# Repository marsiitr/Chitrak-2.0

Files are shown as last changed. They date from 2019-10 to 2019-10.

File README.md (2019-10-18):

# Chitrak-2.0

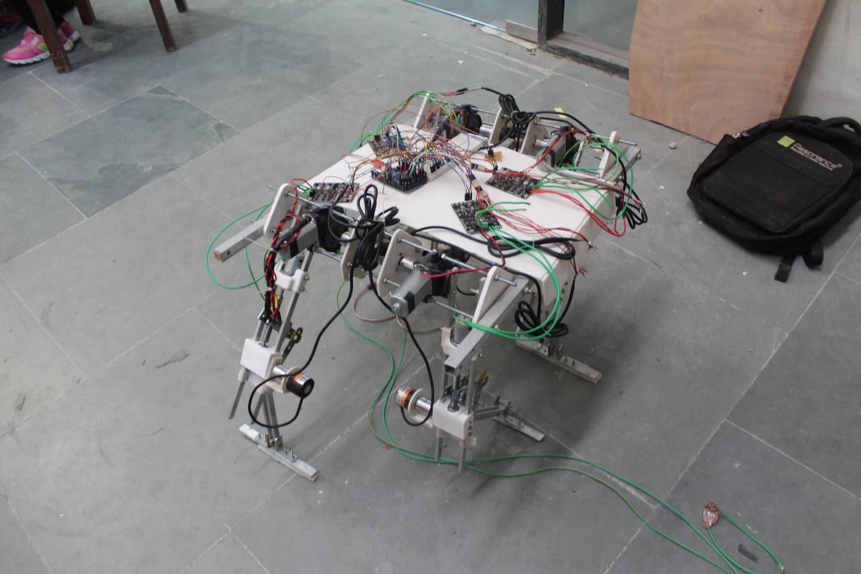
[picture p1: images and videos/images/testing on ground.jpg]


## **Abstract-:**

Chitrak is aimed to be a dynamically stable quadruped robot. With the hopes that it will be able to serve as a robotic cat to accompany soldiers in terrain too rough for conventional vehicles and provide aid to people during natural calamities when conventional vehicles prove to be less usable. Chitrak uses four legs for movement, allowing it to move across surfaces that would defeat wheels.
<br/>

## **Motivation:**

* The current robots being used are very expensive.
* The runtime of the current robots is very less. And on a single charge they cannot be deployed for practical use by the military. 
* Also, when standing, these robot consume energy which can be avoided to increase the runtime.
* Package delivery during Natural disasters can be faster and efficient. 
* Soldiers will be able to carry more food & ammunition during combat missions.
<br/>

## **Mechanical Aspect of the Design:**
As we are designing a fully actuated quadruped so in our first design basically we have used two motors for actuating each joint(hip and knee)of a leg. In the beginning, our main aim was to build quadruped which is both cost effective and energy efficient. So, for that purpose we used a worm geared motor which has a self locking property because of worm gear which can only be able to rotate using worm and so it cannot be back-driven. So it's main advantage will be it does not need to be operating to work against gravity in static position.

<br/>

Next placing both the motors at the hip is self beneficiary as it reduces the amount of torque hip motor has to apply to lift the legs, so  we have mounted both motors on hip. Also for power transmission for motor to  actuate knee joint we have used a timing belt pulley system (as it will have less weight and  it effectively transfers the load). Now on seeing the actual leg motion during walking we see that the upper leg is moving in the direction of gravity while lower leg against it mostly. Therefore we required larger torque to move the lower leg than upper by calculating the approximate torques we have reached on conclusion of using a 1:4 gear ratio belt pulley system so as to increase torque on knee joints

<br/>

Further we have used aluminium links for constructing it ,some 3d printed parts for joints, mountings and 3d printed pulleys. There are two parallel links that are connected through nuts and bolts to provide more stiffness and strength to the structure for upper and lower leg. Rotary encoders are used as a sensors to provide feedback about the position of legs they are mounted on hip joints coupled to each motor. For end effector we used a broad padded plate in order to provide more surface area for better traction. The two front legs are joined using 6mm threaded rod, same is for back legs and these two parts are joined with alumininum channel to construct a body on which whole electronics system is being placed.

<br/>

The problem with this design was that the Belt-Pulley mechanism failed while testing the quadruped on ground. The timing belt was slipping on the upper pulley due to load on the leg during the gait cycle. This slipping changed the angle between the upper and lower leg to an arbitrary value and the whole cycle would get disrupted. 

<br/>

In the current design, we used a lead screw mechanism to drive the lower leg. In it, an 8-cm long lead screw is placed parallel to the upper leg (thigh) and a link is attached to its nut which drives the lower leg. So, the linear motion of the nut on lead screw gets converted to rotational motion of lower leg about the knee joint. Since lead screw mechanism is self locking upto very large amount of load, it can bear the impact loading during the gait cycle and overcomes the problem faced in the previous design.

<br/>

Upper leg in actuated by the same worm-geared motor. Lead Screw is powered by a 900RPM DC geared motor to provide sufficient speed for driving the lower leg. This motor is mounted on the upper leg by a 3D printed part, 'Motor Mount' (solidworks file) containing cavities for the parallel links. Knee joint is also made with 3D printed part, 'Revolute Joint', which contains link spaces and cavities for two radial ball bearings on either side for holding the shaft. A machined Aluminium part is used to couple the lower leg to knee shaft. A Rotary Encoder is also coupled with the Knee Shaft for feedback of the angle between upper and lower leg.

<br/>

## **Electronics Aspect of the Design:**

Chitrak is powered by 4 LiPo batteries(1 for each leg) driving 8 Worm-Gear 500 RPM motors. Each leg has 2 DOF with two actuators (one for the hip joint, and one for each knee joint), for a total of 8 motors. For a single leg, there are 2 active legs joint. The knee joint is rotated by the actuator mounted at hip joint through the belt. Each actuator unit consists of a rotary encoder attached to it for angle measurement.

<br/>

In our first prototype of one leg, we first simulated the motion of the leg on Matlab. By taking the trajectory of the end-effector to be a semi-ellipse (which is the approximate trajectory of natural leg motion), we applied inverse kinematics on the end-effector by considering an X-Y reference frame on the hip joint and varied the joint angles accordingly. For smooth motion, we used Spline for trajectory planning taking the acceleration to be zero. On physical implementation, the leg worked as expected with the end-effector following an ellipse and leg mimicking the motion similar to that of a four-legged animal.

<br/>

For the trajectory, for self-coordinated movement of the four legs, we are using the method of. 2D inverted pendulum method for alternate legs. It consists of the center of mass (CoM) and massless telescopic leg. We measure the inclination of the pendulum θ from vertical, positive for counterclockwise rotation. This yields us the horizontal dynamics of the CoM. The kick force f = Mg/ cos θ always balance with the gravity acting on the point mass. Time for transfer and support leg exchange movement is easily obtained by solving the differential equations of orbital energy and force. Solving these equations helps us to generate the walking pattern generation according to the corresponding gait cycle.

<br/>

For coordinating motion of all three legs, one leg is lifted from the ground at a time and rest of legs are moving in straight line. Thus a straight line has to be broken into 3 parts, and each leg traverses in a different part of straight line while another leg is completing elliptical motion.

<br/>

## **Estimated Budget:**

The Design of Kitty is made with the main focus on lightweight, high endurance and low cost. Most of the components used in the bot are easily accessible. The current estimated cost of Kitty is around 53000 INR. The cost can be significantly reduced when the bot is manufactured commercially on a large scale. It is cheap, easy to reproduce, robust, and safe to handle. This makes it an excellent tool for research of multi-segment legs in quadruped robots.

---------------------------------------------------------
|Component 		 |	Cost(INR) |	Total	 |
|---|---|---|
|Worm Geared Motor (x8)	|	1552 	 |	12417	 |
|LiPo Battery(x5) 	 |	1309 	 |	6545	 |
|Rotary Encoder(x8) 	  |	1590 	 |	12720	 |
|Arduino Uno(x5) 	 |	425 	 | 2125 |
|Cytron Motor Driver(x4)|	1890 	 |	7560	 |
|PCB (x1) 		 |	1000 	 |	1000	 |
|MPU6050 (x2) 		 |	150 	 |	300	 |
|Ultrasonic Sensor (x2) |	197 	 |	394	 |
|Jumper Wires 		|	5 	 |	150	 |
|Square Channels (x20ft)|	20 	 |	400	 |
|Aluminum Links (x12ft) |	20 	 |	320	 |
|Chain & Sprocket (x4) 	|	400 	 |	1600 	|
|3D Printed Parts (x4) 	|	1500 	 |	6000 	|
|Miscellaneous 	 	|	800 	 |	1000	 |
|Total 			 |		 |	52531 |
<br/>

## **Applications:**
* Travel in rough terrains where conventional vehicles have low mobility.
* Carry payloads for soldiers in Combat operations for long duration.
* Provide aid to soldiers during combat operations without loss of human lives.
* Deploy food and medicines to people stuck in inaccessible areas during natural disasters.
<br/>

## **Limitations:**

* Obstacle detection has not been included.
* IMU has not been implemented for self balancing in rough terrain.
* Currently movement of robot is restricted to 1 dimension only.
<br/>

## **Future Goals:**

* Increase Runtime of the Robot after a single charge.
* Obtain Pace, Gallop and Canter Gait cycle for faster movement.
* Increase the Payload Capacity of the Robot.
* Provide 3 DOF to each leg providing more flexibility to the robot.
* Using Computer Vision for Obstacle detection, human recognition and corresponding Path planning.
* Provide 3 DOF to each leg providing more flexibility to the robot.   
<br/>

## **Team Members:**

* Avdesh Ranwa
* Dhruv Sehgal
* Harshil Patel
* Ujjwal Baranwal 
* Yawan Gupta
<br/>

## **Mentros:**

* Divyansh Gupta
* Nitin Yadav
* Prashant Kumar
* Vishal Singh
<br/>

## **References:**
---------------------------------------------------------------------------------
|Name				 |	Author				 	|
|---|---|
|Research of Mammal BionicQuadrupedRobots 	 |Yibin Li, Bin Li, Jiuhong Ruan, and Xuewen Rong Quadruped Walking Robots at Tokyo Institute of	Technology Design, Analysis, and Gait Control Methods SHIGEO HIROSE, YASUSHI FUKUDA, KAN YONEDA, AKIHIKO NAGAKUBO, HIDEYUKI TSUKAGOSHI, KEISUKE ARIKAWA, GEN ENDO, TAKAHIRO DOI, AND RYUICHI HODOSHIMA|
|Kinematic Modeling of Quadruped Robot		 |Smita A. Ganjare, V S Narwane & Ujwal Deole	  |
|Inverse Kinematic Analysis Of A QuadrupedRobot 	  |Muhammed Arif Sen, Veli Bakırcıoğlu, Mete Kalyoncu|
|Introduction to Robotics	 |John J. Craig		 |
|Robot Dynamics and Control	 |Mark W. Spong, M. Vidyasagar, Seth Hutchinson  |

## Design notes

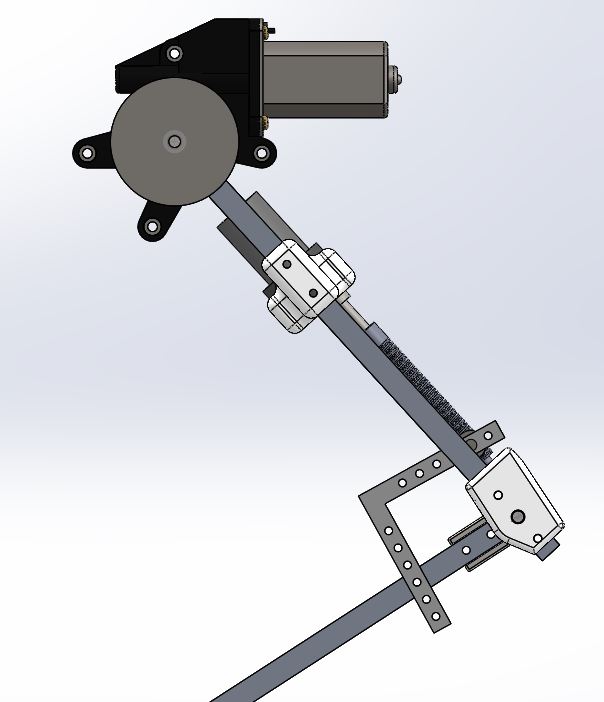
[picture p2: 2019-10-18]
images and videos/images/leg design.jpeg

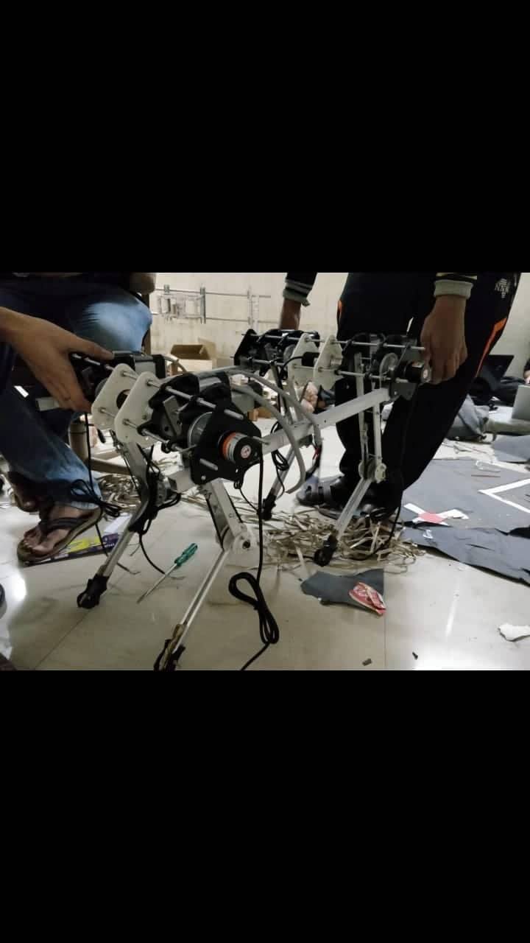
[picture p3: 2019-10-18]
images and videos/images/second design.jpg

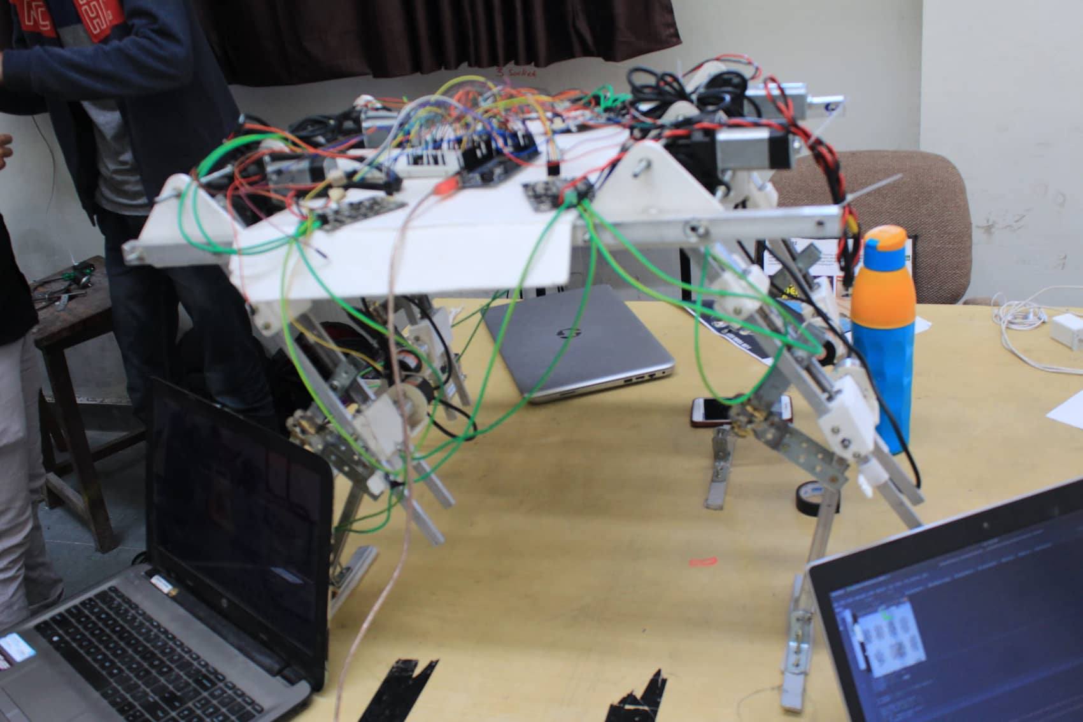
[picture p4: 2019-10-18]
images and videos/images/chitrak current design.jpg

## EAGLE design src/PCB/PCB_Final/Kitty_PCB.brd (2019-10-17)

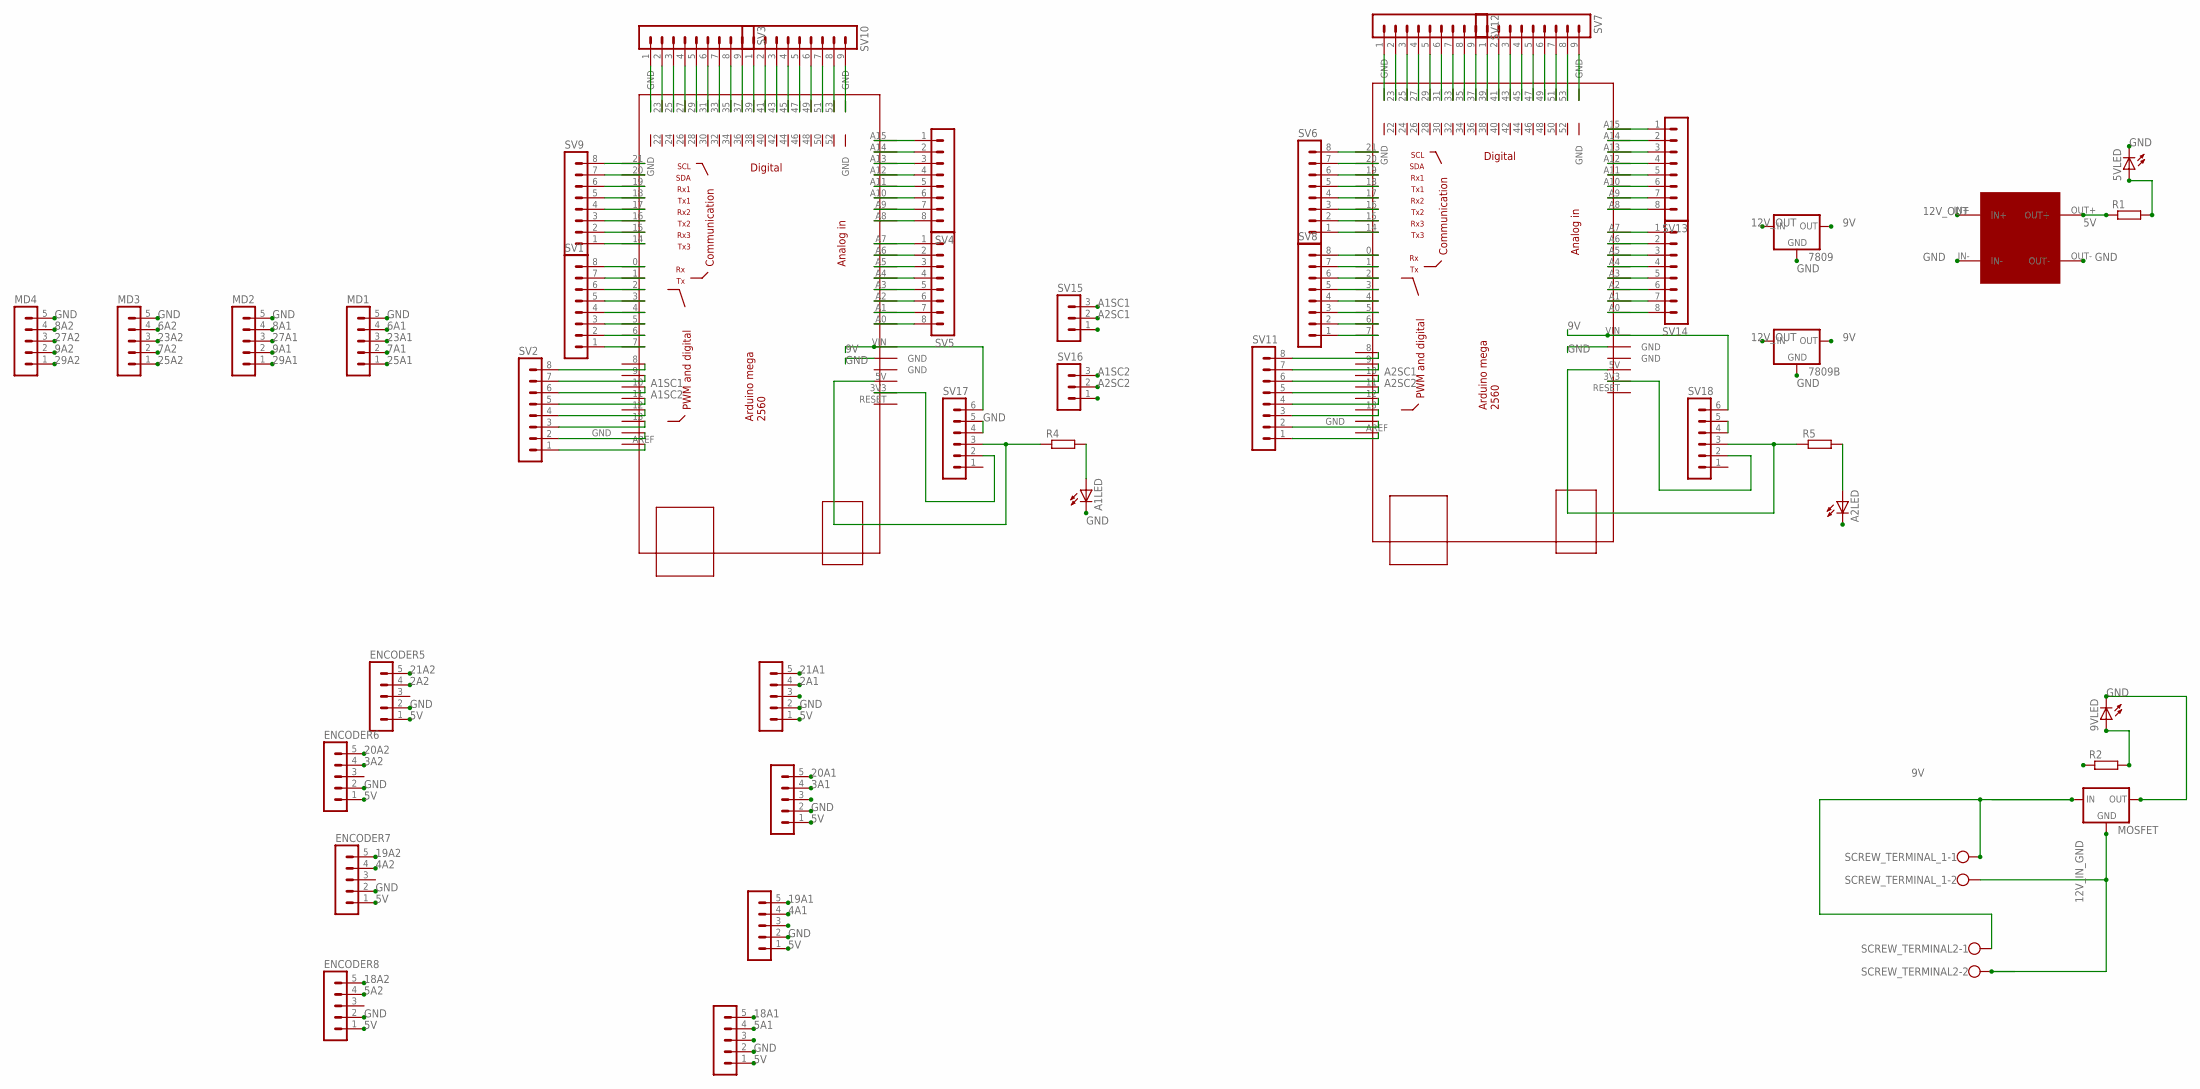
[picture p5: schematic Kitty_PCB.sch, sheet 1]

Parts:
5VLED, 9VLED: LED; LED3MM
7809, 7809B: VOLTAGE_REGULATOR_78XXS; 78XXS
A1LED, A2LED: LED; LED3MM
ARDUINO1, ARDUINO2: MEGA_DEVICE; MEGABOX
ENCODER1, ENCODER2, ENCODER3, ENCODER4, ENCODER5, ENCODER6, ENCODER7, ENCODER8: RELIMATE_05-1; MA05-1
MD1, MD2, MD3, MD4: RELIMATE_05-1; MA05-1
MOSFET: VOLTAGE_REGULATOR_78XXS; 78XXS
R1, R2, R4, R5: RESISTANCE0207/10; 0207/10
SCREW_TERMINAL2: SCREW_TERMINAL_POWER; POWER_CONNECTOR
SCREW_TERMINAL_1: SCREW_TERMINAL_POWER; POWER_CONNECTOR
SV1, SV2, SV4, SV5, SV6, SV8, SV9, SV11, SV13, SV14: RELIMATE_08-1; MA08-1
SV3, SV7, SV10, SV12: RELIMATE_09-1; MA09-1
SV15, SV16: RELIMATE_03-1; MA03-1
SV17, SV18: RELIMATE_06-1; MA06-1
U$1: BUCK_CONVERTER

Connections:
0A1: ARDUINO1.0, SV1.8
0A2: ARDUINO2.0, SV8.8
1A1: ARDUINO1.1, SV1.7
1A2: ARDUINO2.1, SV8.7
2A1: ARDUINO1.2, ENCODER1.4, SV1.6
2A2: ARDUINO2.2, ENCODER5.4, SV8.6
3A1: ARDUINO1.3, ENCODER2.4, SV1.5
3A2: ARDUINO2.3, ENCODER6.4, SV8.5
4A1: ARDUINO1.4, ENCODER3.4, SV1.4
4A2: ARDUINO2.4, ENCODER7.4, SV8.4
5A1: ARDUINO1.5, ENCODER4.4, SV1.3
5A2: ARDUINO2.5, ENCODER8.4, SV8.3
5V: ENCODER1.1, ENCODER2.1, ENCODER3.1, ENCODER4.1, ENCODER5.1, ENCODER6.1, ENCODER7.1, ENCODER8.1, R1.1, U$1.OUT+
6A1: ARDUINO1.6, MD1.4, SV1.2
6A2: ARDUINO2.6, MD3.4, SV8.2
7A1: ARDUINO1.7, MD1.2, SV1.1
7A2: ARDUINO2.7, MD3.2, SV8.1
8A1: ARDUINO1.8, MD2.4, SV2.8
8A2: ARDUINO2.8, MD4.4, SV11.8
9A1: MD2.2
9A2: ARDUINO1.9, ARDUINO2.9, MD4.2, SV2.7, SV11.7
9V: 7809.OUT, 7809B.OUT, ARDUINO1.VIN, ARDUINO2.VIN, R2.1, SV17.6, SV18.6
12A1: ARDUINO1.12, SV2.4
12A2: ARDUINO2.12, SV11.4
12V_IN_GND: MOSFET.GND, SCREW_TERMINAL2.2, SCREW_TERMINAL_1.2
12V_OUT: 7809.IN, 7809B.IN, MOSFET.IN, SCREW_TERMINAL2.1, SCREW_TERMINAL_1.1, U$1.IN+
13A1: ARDUINO1.13, SV2.3
13A2: ARDUINO2.13, SV11.3
14A1: ARDUINO1.14, SV9.1
14A2: ARDUINO2.14, SV6.1
15A1: ARDUINO1.15, SV9.2
15A2: ARDUINO2.15, SV6.2
16A1: ARDUINO1.16, SV9.3
16A2: ARDUINO2.16, SV6.3
17A1: ARDUINO1.17, SV9.4
17A2: ARDUINO2.17, SV6.4
18A1: ARDUINO1.18, ENCODER4.5, SV9.5
18A2: ARDUINO2.18, ENCODER8.5, SV6.5
19A1: ARDUINO1.19, ENCODER3.5, SV9.6
19A2: ARDUINO2.19, ENCODER7.5, SV6.6
20A1: ARDUINO1.20, ENCODER2.5, SV9.7
20A2: ARDUINO2.20, ENCODER6.5, SV6.7
21A1: ARDUINO1.21, ENCODER1.5, SV9.8
21A2: ARDUINO2.21, ENCODER5.5, SV6.8
23A1: ARDUINO1.23, MD1.3, SV3.2
23A2: ARDUINO2.23, MD3.3, SV12.2
25A1: ARDUINO1.25, MD1.1, SV3.3
25A2: ARDUINO2.25, MD3.1, SV12.3
27A1: ARDUINO1.27, MD2.3, SV3.4
27A2: ARDUINO2.27, MD4.3, SV12.4
29A1: ARDUINO1.29, MD2.1, SV3.5
29A2: ARDUINO2.29, MD4.1, SV12.5
31A1: ARDUINO1.31, SV3.6
31A2: ARDUINO2.31, SV12.6
33A1: ARDUINO1.33, SV3.7
33A2: ARDUINO2.33, SV12.7
35A1: ARDUINO1.35, SV3.8
35A2: ARDUINO2.35, SV12.8
37A1: ARDUINO1.37, SV3.9
37A2: ARDUINO2.37, SV12.9
A1SC1: ARDUINO1.10, SV2.6, SV15.3
A1SC2: ARDUINO1.11, SV2.5, SV16.3
A2SC1: ARDUINO2.10, SV11.6, SV15.2
A2SC2: ARDUINO2.11, SV11.5, SV16.2
GND: 5VLED.K (C), 9VLED.K (C), 7809.GND, 7809B.GND, A1LED.K (C), A2LED.K (C), ARDUINO1.GND@3 (GND), ARDUINO2.GND@3 (GND), ENCODER1.2, ENCODER2.2, ENCODER3.2, ENCODER4.2, ENCODER5.2, ENCODER6.2, ENCODER7.2, ENCODER8.2, MD1.5, MD2.5, MD3.5, MD4.5, MOSFET.OUT, SV17.4, SV17.5, U$1.IN-, U$1.OUT-
unnamed: ARDUINO1.3V3, SV17.2
unnamed: ARDUINO1.5V, R4.1, SV17.3
unnamed: 5VLED.A, R1.2
unnamed: SV18.4, SV18.5
unnamed: ARDUINO2.3V3, SV18.2
unnamed: ARDUINO2.5V, R5.1, SV18.3
unnamed: A1LED.A, R4.2
unnamed: A2LED.A, R5.2
unnamed: 9VLED.A, R2.2
unnamed: ARDUINO1.GND@5 (GND), SV3.1
unnamed: ARDUINO1.GND@1 (GND), SV2.2
unnamed: ARDUINO1.AREF, SV2.1
unnamed: ARDUINO1.A15, SV4.1
unnamed: ARDUINO1.A14, SV4.2
unnamed: ARDUINO1.A13, SV4.3
unnamed: ARDUINO1.A12, SV4.4
unnamed: ARDUINO1.A11, SV4.5
unnamed: ARDUINO1.A10, SV4.6
unnamed: ARDUINO1.A9, SV4.7
unnamed: ARDUINO1.A8, SV4.8
unnamed: ARDUINO1.A7, SV5.1
unnamed: ARDUINO1.A6, SV5.2
unnamed: ARDUINO1.A5, SV5.3
unnamed: ARDUINO1.A4, SV5.4
unnamed: ARDUINO1.A3, SV5.5
unnamed: ARDUINO1.A2, SV5.6
unnamed: ARDUINO1.A1, SV5.7
unnamed: ARDUINO1.A0, SV5.8
unnamed: ARDUINO2.GND@1 (GND), SV11.2
unnamed: ARDUINO2.AREF, SV11.1
unnamed: ARDUINO2.A15, SV13.1
unnamed: ARDUINO2.A14, SV13.2
unnamed: ARDUINO2.A13, SV13.3
unnamed: ARDUINO2.A12, SV13.4
unnamed: ARDUINO2.A11, SV13.5
unnamed: ARDUINO2.A10, SV13.6
unnamed: ARDUINO2.A9, SV13.7
unnamed: ARDUINO2.A8, SV13.8
unnamed: ARDUINO2.A7, SV14.1
unnamed: ARDUINO2.A6, SV14.2
unnamed: ARDUINO2.A5, SV14.3
unnamed: ARDUINO2.A4, SV14.4
unnamed: ARDUINO2.A3, SV14.5
unnamed: ARDUINO2.A2, SV14.6
unnamed: ARDUINO2.A1, SV14.7
unnamed: ARDUINO2.A0, SV14.8
unnamed: ARDUINO1.39, SV10.1
unnamed: ARDUINO1.41, SV10.2
unnamed: ARDUINO1.43, SV10.3
unnamed: ARDUINO1.45, SV10.4
unnamed: ARDUINO1.47, SV10.5
unnamed: ARDUINO1.49, SV10.6
unnamed: ARDUINO1.51, SV10.7
unnamed: ARDUINO1.53, SV10.8
unnamed: ARDUINO1.GND@7 (GND), SV10.9
unnamed: ARDUINO2.GND@5 (GND), SV12.1
unnamed: ARDUINO2.39, SV7.1
unnamed: ARDUINO2.41, SV7.2
unnamed: ARDUINO2.43, SV7.3
unnamed: ARDUINO2.45, SV7.4
unnamed: ARDUINO2.47, SV7.5
unnamed: ARDUINO2.49, SV7.6
unnamed: ARDUINO2.51, SV7.7
unnamed: ARDUINO2.53, SV7.8
unnamed: ARDUINO2.GND@7 (GND), SV7.9

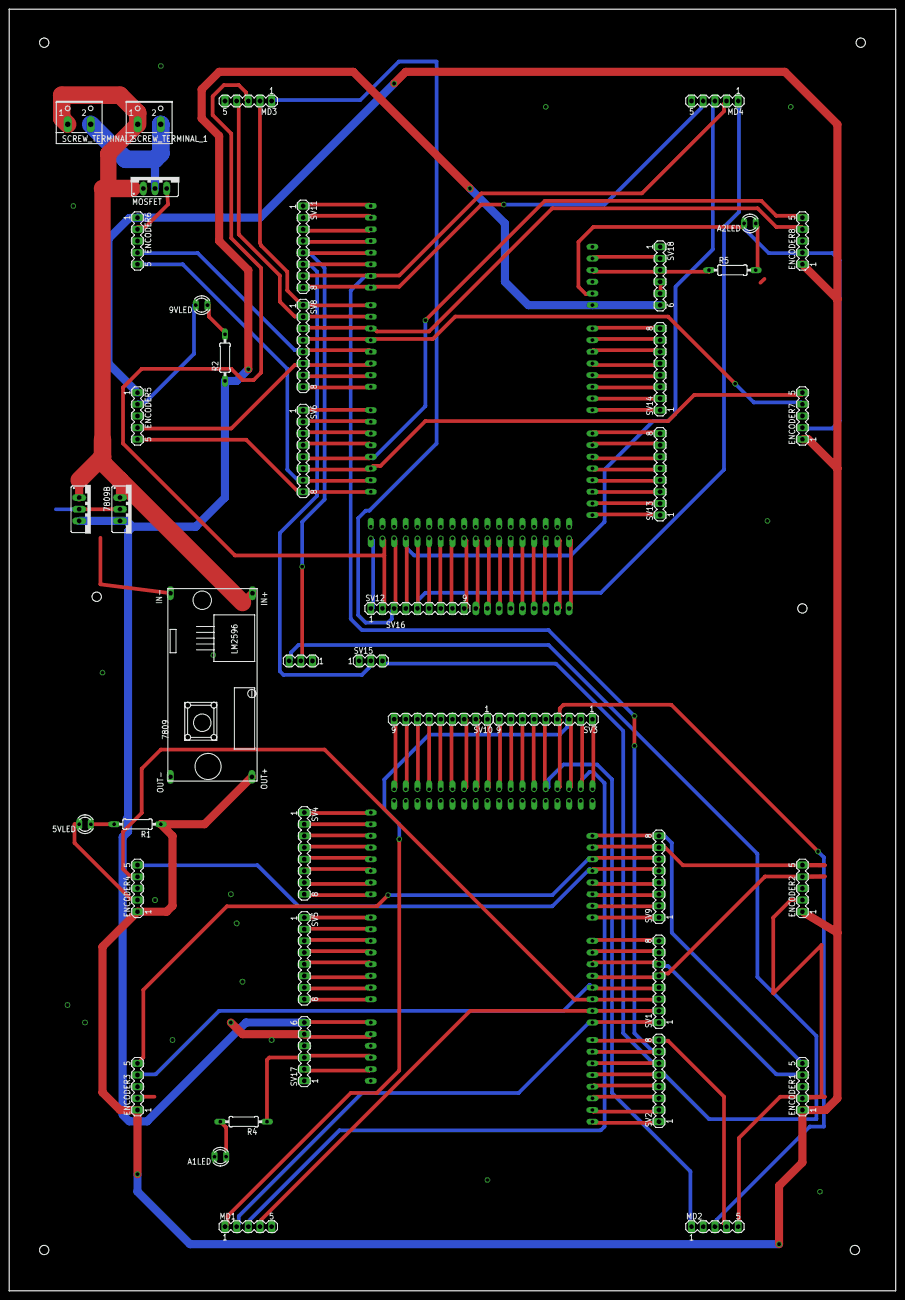
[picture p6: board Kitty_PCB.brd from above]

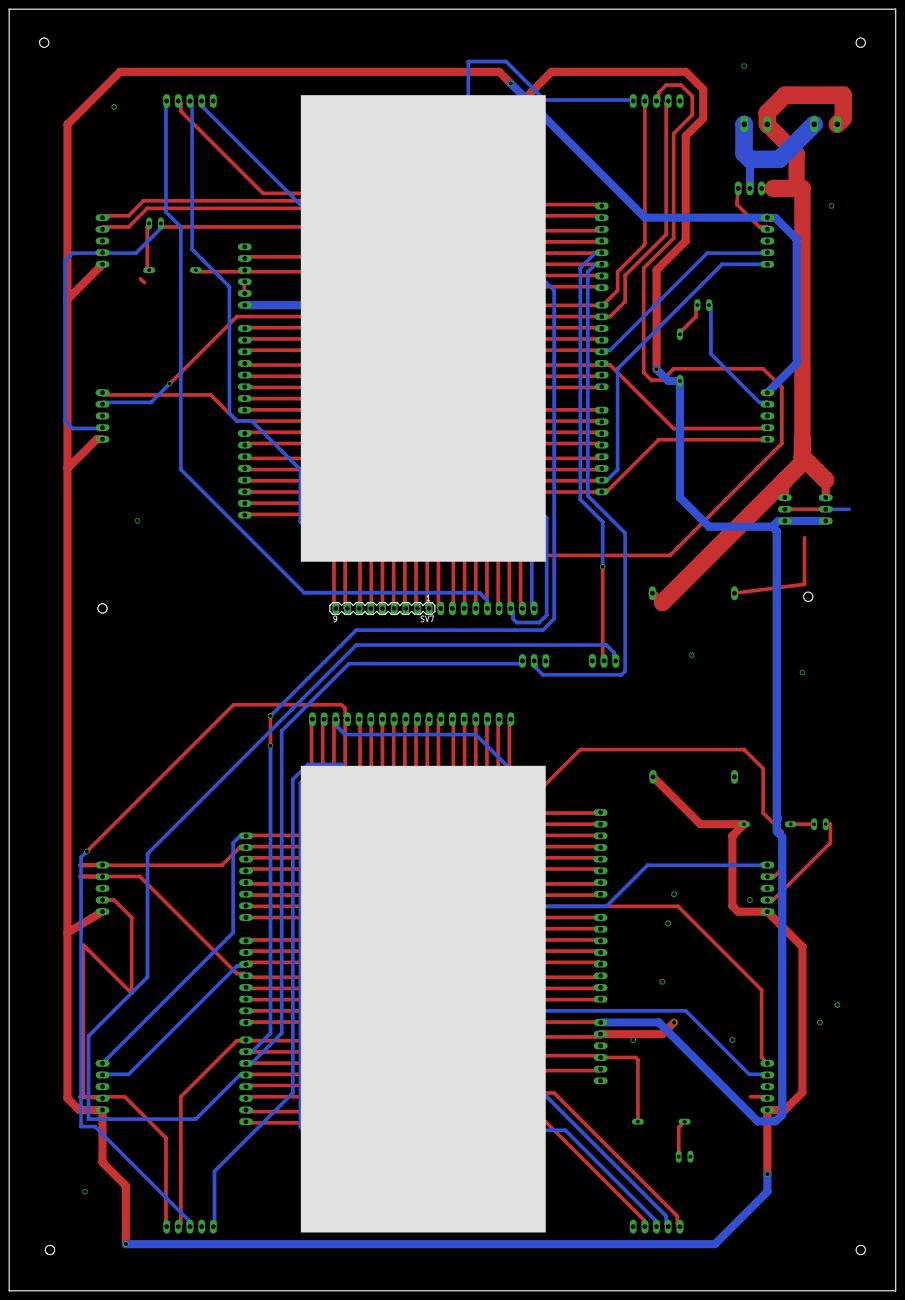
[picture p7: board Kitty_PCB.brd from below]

Board: 2 copper layers, 193.0 x 279.1 mm, 46 parts (3 on the bottom side), 129 nets.

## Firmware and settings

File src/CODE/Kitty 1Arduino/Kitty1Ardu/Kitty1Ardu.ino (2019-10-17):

#include <PinChangeInt.h>

#define a1_1 20
#define a2_1 19
#define a1_2 21
#define a2_2 A11
#define a1_3 3
#define a2_3 A12
#define a1_4 18
#define a2_4 A14

int A1_1 = 3, A1_2 = 2, A1_3 = 1, A1_4 = 5;
int A2_1 = 4;
#define b1_1 A15
#define b2_1 51
#define b1_2 A2
#define b2_2 A0
#define b1_3 48
#define b2_3 53
#define b1_4 52
#define b2_4 47

#define motor1_1  43
#define motor2_1  40
#define motor1pwm_1  2
#define motor2pwm_1  11

#define motor1_2  31
#define motor2_2  29
#define motor1pwm_2  5
#define motor2pwm_2  10

#define motor1_3  14
#define motor2_3  22
#define motor1pwm_3  6
#define motor2pwm_3  7

#define motor1_4  36
#define motor2_4  37
#define motor1pwm_4  8
#define motor2pwm_4  9

bool state1_1 = true;
bool state2_1 = true;
bool state1_2 = true;
bool state2_2 = true;
bool state1_3 = true;
bool state2_3 = true;
bool state1_4 = true;
bool state2_4 = true;

double alpha_1;
double w = 0.1, theta1c_1 = 0.0 , theta2c_1 = 0.0, theta1_1, theta2_1, error1_1, error2_1, correction1_1, correction2_1, c1_1, c2_1;
double dif_error1_1 , prev_error1_1 = 0.0 , dif_error2_1 , prev_error2_1 = 0.0;

double alpha_2;
double theta1c_2 = 0.0 , theta2c_2 = 0.0, theta1_2, theta2_2, error1_2, error2_2, correction1_2, correction2_2, c1_2, c2_2;
double dif_error1_2 , prev_error1_2 = 0.0 , dif_error2_2 , prev_error2_2 = 0.0;

double alpha_3, theta1c_3 = 0.0 , theta2c_3 = 0.0, theta1_3, theta2_3, error1_3, error2_3, correction1_3, correction2_3, c1_3, c2_3;
double dif_error1_3 , prev_error1_3 = 0.0 , dif_error2_3 , prev_error2_3 = 0.0;

double alpha_4, theta1c_4 = 0.0 , theta2c_4 = 0.0, theta1_4, theta2_4, error1_4, error2_4, correction1_4, correction2_4, c1_4, c2_4;
double dif_error1_4 , prev_error1_4 = 0.0 , dif_error2_4 , prev_error2_4 = 0.0;

volatile int temp1_1 , counter1_1 = 0;
volatile int temp2_1 , counter2_1 = 0;

volatile int temp1_2 , counter1_2 = 0;
volatile int temp2_2 , counter2_2 = 0;

volatile int temp1_3 , counter1_3 = 0;
volatile int temp2_3 , counter2_3 = 0;

volatile int temp1_4 , counter1_4 = 0;
volatile int temp2_4 , counter2_4 = 0;

double Kp1 = 1.5, Kp2 = 1.5, Kd1 = 2.0, Kd2 = 2.0 ;
int l1 = 25, l2 = 25;

double theta1AT1 = 53.728, theta1AT2 = 45.78, theta1AT3 = 69.71, theta1_AT1 = 0, theta1_AT2 = 0.1, theta1_AT3 = 0, theta1__AT1 = 0, theta1__AT2 = 0.1, theta1__AT3 = 0;
double theta2AT1 = 42.68, theta2AT2 = 76.73, theta2AT3 = 50.75, theta2_AT1 = 0, theta2_AT2 = 0.1, theta2_AT3 = 0, theta2__AT1 = 0, theta2__AT2 = 0.1, theta2__AT3 = 0;

double theta1AT1_2 = 54.68, theta1AT2_2 = 48.41, theta1AT3_2 = 72.815, theta1_AT1_2 = 0, theta1_AT2_2 = 0.1, theta1_AT3_2 = 0, theta1__AT1_2 = 0, theta1__AT2_2 = 0.1, theta1__AT3_2 = 0;
double theta2AT1_2 = 45.57, theta2AT2_2 = 77.29, theta2AT3_2 = 49.55, theta2_AT1_2 = 0, theta2_AT2_2 = 0.1, theta2_AT3_2 = 0, theta2__AT1_2 = 0, theta2__AT2_2 = 0.1, theta2__AT3_2 = 0;

double theta1AT1_3=53.728,theta1AT2_3=45.78,theta1AT3_3=69.71,theta1_AT1_3=0,theta1_AT2_3=0.1,theta1_AT3_3=0,theta1__AT1_3=0,theta1__AT2_3=0.1,theta1__AT3_3=0;
double theta2AT1_3=42.68,theta2AT2_3=76.73,theta2AT3_3=50.75,theta2_AT1_3=0,theta2_AT2_3=0.1,theta2_AT3_3=0,theta2__AT1_3=0,theta2__AT2_3=0.1,theta2__AT3_3=0;

double theta1AT1_4=54.68,theta1AT2_4=48.41,theta1AT3_4=72.815,theta1_AT1_4=0,theta1_AT2_4=0.1,theta1_AT3_4=0,theta1__AT1_4=0,theta1__AT2_4=0.1,theta1__AT3_4=0;
double theta2AT1_4=45.57,theta2AT2_4=77.29,theta2AT3_4=49.55,theta2_AT1_4=0,theta2_AT2_4=0.1,theta2_AT3_4=0,theta2__AT1_4=0,theta2__AT2_4=0.1,theta2__AT3_4=0;

void setup()
{
  Serial.begin(9600);
  pinMode(a1_1, INPUT_PULLUP);
  pinMode(a2_1, INPUT_PULLUP);
  pinMode(a1_2, INPUT_PULLUP);
  pinMode(a2_2, INPUT_PULLUP);
  pinMode(a1_3, INPUT_PULLUP);
  pinMode(a2_3, INPUT_PULLUP);
  pinMode(a1_4, INPUT_PULLUP);
  pinMode(a2_4, INPUT_PULLUP);

  pinMode(b1_1, INPUT_PULLUP);
  pinMode(b2_1, INPUT_PULLUP);
  pinMode(b1_2, INPUT_PULLUP);
  pinMode(b2_2, INPUT_PULLUP);
  pinMode(b1_3, INPUT_PULLUP);
  pinMode(b2_3, INPUT_PULLUP);
  pinMode(b1_4, INPUT_PULLUP);
  pinMode(b2_4, INPUT_PULLUP);

  attachInterrupt(A1_1, ai1_1, CHANGE);
  attachInterrupt(A2_1, ai2_1, CHANGE);
  attachInterrupt(A1_2, ai1_2, CHANGE);
  PCintPort::attachInterrupt(a2_2, ai2_2, CHANGE);
  attachInterrupt(A1_3, ai1_3, CHANGE);
  PCintPort::attachInterrupt(a2_3, ai2_3, CHANGE);
  attachInterrupt(A1_4, ai1_4, CHANGE);
  PCintPort::attachInterrupt(a2_4, ai2_4, CHANGE);
  state1_1 = digitalRead(a1_1);
  state2_1 = digitalRead(a2_1);
  state1_2 = digitalRead(a1_2);
  state2_2 = digitalRead(a2_2);
  state1_3 = digitalRead(a1_3);
  state2_3 = digitalRead(a2_3);
  state1_4 = digitalRead(a1_4);
  state2_4 = digitalRead(a2_4);

  pinMode(motor1_1, OUTPUT);
  pinMode(motor1pwm_1, OUTPUT);
  pinMode(motor2_1, OUTPUT);
  pinMode(motor2pwm_1, OUTPUT);

  pinMode(motor1_2, OUTPUT);
  pinMode(motor1pwm_2, OUTPUT);
  pinMode(motor2_2, OUTPUT);
  pinMode(motor2pwm_2, OUTPUT);
  
  pinMode(motor1_3, OUTPUT);
  pinMode(motor1pwm_3, OUTPUT);
  pinMode(motor2_3, OUTPUT);
  pinMode(motor2pwm_3, OUTPUT);

  pinMode(motor1_4, OUTPUT);
  pinMode(motor1pwm_4, OUTPUT);
  pinMode(motor2_4, OUTPUT);
  pinMode(motor2pwm_4, OUTPUT);
}

void loop()
{
  for (double t = 0.1666, u = 0.887; t < 1, u < 5.333; t = t + 0.1666, u = u + 0.887)
  {
    double xe_2 = 4.66 + u ;
    double ye_2 = -45 ;

    double xe_3 = 1.3333 + u ;
    double ye_3 = -45 ;

    double xe_4 = -6 + u ;
    double ye_4 = -45;

    if ( counter1_1 != temp1_1 ) {
      temp1_1 = counter1_1;

      if (counter1_1 > 1200)
      {
        counter1_1 = 0;
      }
      theta1c_1 = (counter1_1 * 0.3);
    }

    if ( counter2_1 != temp2_1 ) {
      temp2_1 = counter2_1;

      if (counter2_1 > 1200)
      {
        counter2_1 = 0;
      }
      theta2c_1 = (counter2_1 * 0.3);
    }

    if ( counter1_2 != temp1_2 ) {
      temp1_2 = counter1_2;

      if (counter1_2 > 1200) {
        counter1_2 = 0;
      }

      theta1c_2 = (counter1_2 * 0.3);
    }

    if ( counter2_2 != temp2_2 ) {
      temp2_2 = counter2_2;

      if (counter2_2 > 1200) {
        counter2_2 = 0;
      }
      theta2c_2 = -(counter2_2 * 0.3);
    }

    if ( counter1_3 != temp1_3 ) {
      temp1_3 = counter1_3;

      if (counter1_3 > 1200)
        counter1_3 = 0;

      theta1c_3 = (counter1_3 * 0.3);
    }

    if ( counter2_3 != temp2_3 ) {
      temp2_3 = counter2_3;

      if (counter2_3 > 1200)
        counter2_3 = 0;

      theta2c_3 = -(counter2_3 * 0.3);
    }

    if ( counter1_4 != temp1_4 ) {
      temp1_4 = counter1_4;

      if (counter1_4 > 1200)
        counter1_4 = 0;

      theta1c_4 = (counter1_4 * 0.3);
    }

    if ( counter2_4 != temp2_4 ) {
      temp2_4 = counter2_4;

      if (counter2_4 > 1200)
        counter2_4 = 0;

      theta2c_4 = -(counter2_4 * 0.3);
    }


    if (atan(ye_2 / xe_2) > 0)
      alpha_2 = atan(ye_2 / xe_2) - 3.14159;

    else
      alpha_2 = atan(ye_2 / xe_2);

    if (atan(ye_3 / xe_3) > 0)
      alpha_3 = atan(ye_3 / xe_3) - PI;

    else
      alpha_3 = atan(ye_3 / xe_3);

    if (atan(ye_4 / xe_4) > 0)
      alpha_4 = atan(ye_4 / xe_4) - PI;

    else
      alpha_4 = atan(ye_4 / xe_4);

    //----------------------------------------------1111111111111111111------------------------------------------------------------------

    if (t < 0.5) {
      theta1_1 = (-1) * theta(theta1AT1, theta1_AT1, theta1__AT1, theta1AT2, theta1_AT2, theta1__AT2, t);
      theta2_1 = (-1) * theta(theta2AT1, theta2_AT1, theta2__AT1, theta2AT2, theta2_AT2, theta2__AT2, t);
    }
    else {
      theta1_1 = (-1) * theta(theta1AT2, theta1_AT2, theta1__AT2, theta1AT3, theta1_AT3, theta1__AT3, t - 0.5);
      theta2_1 = (-1) * theta(theta2AT2, theta2_AT2, theta2__AT2, theta2AT3, theta2_AT3, theta2__AT3, t - 0.5);
    }

    error1_1 = theta1_1 - theta1c_1 + 53.728;
    error2_1 = theta2_1 - theta2c_1 / 4 + 42.68;

    dif_error1_1 = error1_1 - prev_error1_1;
    dif_error2_1 = error2_1 - prev_error2_1;

    if (t < 0.5)
      c1_1 = (Kp1 - 0.5) * error1_1 + Kd1 * (dif_error1_1);
    else
      c1_1 = (Kp1 - 0.9) * error1_1 + Kd1 * (dif_error1_1);

    c2_1 = Kp2 * error2_1 + Kd2 * (dif_error2_1);

    prev_error1_1 = error1_1;
    prev_error2_1 = error2_1;

    correction1_1 = map(abs(c1_1), 0, 70, 0, 80);
    if (t < 0.5)
      correction2_1 = map(abs(c2_1), 0, 90, 0, 220);
    else
      correction2_1 = map(abs(c2_1), 0, 90, 0, 225);

    //------------------------------------------------22222222222222-------------------------------------------------------------------------

    theta1_2 = 57.2958 * (cosine_rule(l2, l1, sqrt((xe_2 * xe_2) + (ye_2 * ye_2))) + alpha_2);
    theta2_2 = 57.2958 * (-3.14159 + cosine_rule(sqrt(xe_2 * xe_2 + ye_2 * ye_2), l1, l2));

    error1_2 = theta1_2 - theta1c_2 + 65.8795;
    error2_2 = theta2_2 - theta2c_2 / 4 + 50.4;

    dif_error1_2 = error1_2 - prev_error1_2;
    dif_error2_2 = error2_2 - prev_error2_2;

    c1_2 = (Kp1 - 0.5) * error1_2 + (Kd1 + 0.5) * (dif_error1_2);
    c2_2 = Kp2 * error2_2 + Kd2 * (dif_error2_2);

    prev_error1_2 = error1_2;
    prev_error2_2 = error2_2;

    correction1_2 = map(abs(c1_2), 0, 30, 0, 50);     //50
    correction2_2 = map(abs(c2_2), 0, 35, 0, 150);    //175

    //----------------------------------------------3333333333333333333333--------------------------------------------------------------------

    theta1_3 = 57.2958 * (cosine_rule(l2, l1, sqrt((xe_3 * xe_3) + (ye_3 * ye_3))) + alpha_3);
    theta2_3 = 57.2958 * (-3.14159 + cosine_rule(sqrt(xe_3 * xe_3 + ye_3 * ye_3), l1, l2));


    error1_3 = theta1_3 - theta1c_3 + 62.513;
    error2_3 = theta2_3 - theta2c_3 / 4 + 51.58;

    dif_error1_3 = error1_3 - prev_error1_3;
    prev_error1_3 = error1_3;
    dif_error2_3 = error2_3 - prev_error2_3;
    prev_error2_3 = error2_3;

    c1_3 = (Kp1 - 0.5) * error1_3 + (Kd1 + 0.5) * (dif_error1_3);
    c2_3 = Kp2 * error2_3 + Kd2 * (dif_error2_3);

    correction1_3 = map(abs(c1_3), 0, 30, 0, 50); //50
    correction2_3 = map(abs(c2_3), 0, 35, 0, 150);//175

    //----------------------------------------------------44444444444444444444-----------------------------------------------------------------------

    theta1_4 = 57.2958 * (cosine_rule(l2, l1, sqrt((xe_4 * xe_4) + (ye_4 * ye_4))) + alpha_4);
    theta2_4 = 57.2958 * (-3.14159 + cosine_rule(sqrt(xe_4 * xe_4 + ye_4 * ye_4), l1, l2));

    error1_4 = theta1_4 - theta1c_4 + 72.815;
    error2_4 = theta2_4 - theta2c_4 / 4 + 49.55;

    dif_error1_4 = error1_4 - prev_error1_4;
    prev_error1_4 = error1_4;
    dif_error2_4 = error2_4 - prev_error2_4;
    prev_error2_4 = error2_4;

    c1_4 = (Kp1 - 0.5) * error1_4 + (Kd1 + 0.5) * (dif_error1_4);
    c2_4 = Kp2 * error2_4 + Kd2 * (dif_error2_4);

    correction1_4 = map(abs(c1_4), 0, 30, 0, 50);     //50
    correction2_4 = map(abs(c2_4), 0, 35, 0, 150);    //175

    Serial.print("theta1_1=");
    Serial.println(theta1_1);
    Serial.print("theta1c_1=");
    Serial.println(theta1c_1 - 53.728);
    Serial.print("theta2c_1=");
    Serial.println(theta2c_1 - 42.68);
    Serial.print("theta2_1=");
    Serial.println(theta2_1);
    Serial.print("c1_1=");
    Serial.println(c1_1);
    Serial.print("c2_1=");
    Serial.println(c2_1);
    Serial.print("pwm1=");
    Serial.println(correction1_1);
    Serial.print("pwm2=");
    Serial.println(correction2_1);
    Serial.println("------------------------");


    if (error1_1 < 0 ) {
      upr_mtr_fwd_1();
      analogWrite(motor1pwm_1, abs(correction1_1));
    }

    else if (error1_1 > 0) {
      upr_mtr_bwd_1();
      analogWrite(motor1pwm_1, abs(correction1_1));
    }

    if (error2_1 < 0) {
      lwr_mtr_fwd_1();
      analogWrite(motor2pwm_1, abs(correction2_1));
    }

    else if (error2_1 > 0) {
      lwr_mtr_bwd_1();
      analogWrite(motor2pwm_1, abs(correction2_1));
    }

    if (error1_2 < 0 ) {
      upr_mtr_fwd_2();
      analogWrite(motor1pwm_2, abs(correction1_2));
    }

    else if (error1_2 > 0) {
      upr_mtr_bwd_2();
      analogWrite(motor1pwm_2, abs(correction1_2));
    }

    if (error2_2 < 0) {
      lwr_mtr_fwd_2();
      analogWrite(motor2pwm_2, abs(correction2_2));
    }

    else if (error2_2 > 0) {
      lwr_mtr_bwd_2();
      analogWrite(motor2pwm_2, abs(correction2_2));
    }

    if (error1_3 < 0 ) {
      upr_mtr_fwd_3();
      analogWrite(motor1pwm_3, abs(correction1_3));
    }

    else if (error1_3 > 0) {
      upr_mtr_bwd_3();
      analogWrite(motor1pwm_3, abs(correction1_3));
    }

    if (error2_3 < 0) {
      lwr_mtr_fwd_3();
      analogWrite(motor2pwm_3, abs(correction2_3));
    }

    else if (error2_3 > 0) {
      lwr_mtr_bwd_3();
      analogWrite(motor2pwm_3, abs(correction2_3));
    }

    if (error1_4 < 0 ) {
      upr_mtr_fwd_4();
      analogWrite(motor1pwm_4, abs(correction1_4));
    }

    else if (error1_4 > 0) {
      upr_mtr_bwd_4();
      analogWrite(motor1pwm_4, abs(correction1_4));
    }

    if (error2_4 < 0) {
      lwr_mtr_fwd_4();
      analogWrite(motor2pwm_4, abs(correction2_4));
    }

    else if (error2_4 > 0) {
      lwr_mtr_bwd_4();
      analogWrite(motor2pwm_4, abs(correction2_4));
    }

  }

  for (double t = 0.1666, u = 0.887; t < 1, u < 5.333; t = t + 0.1666, u = u + 0.887)
  {

    double xe_1 = -4 + u ;
    double ye_1 = -45 ;

    double xe_3 = 1.3333 + u + 5.3333 ;
    double ye_3 = -45 ;

    double xe_4 = -6 + u + 5.3333;
    double ye_4 = -45;

    if ( counter1_1 != temp1_1 ) {
      temp1_1 = counter1_1;

      if (counter1_1 > 1200)
      {
        counter1_1 = 0;
      }
      theta1c_1 = (counter1_1 * 0.3);
    }

    if ( counter2_1 != temp2_1 ) {
      temp2_1 = counter2_1;

      if (counter2_1 > 1200)
      {
        counter2_1 = 0;
      }
      theta2c_1 = (counter2_1 * 0.3);
    }

    if ( counter1_2 != temp1_2 ) {
      temp1_2 = counter1_2;

      if (counter1_2 > 1200) {
        counter1_2 = 0;
      }

      theta1c_2 = (counter1_2 * 0.3);
    }

    if ( counter2_2 != temp2_2 ) {
      temp2_2 = counter2_2;

      if (counter2_2 > 1200)
      {
        counter2_2 = 0;
      }
      theta2c_2 = -(counter2_2 * 0.3);
    }

    if ( counter1_3 != temp1_3 ) {
      temp1_3 = counter1_3;

      if (counter1_3 > 1200)
        counter1_3 = 0;

      theta1c_3 = (counter1_3 * 0.3);
    }

    if ( counter2_3 != temp2_3 ) {
      temp2_3 = counter2_3;

      if (counter2_3 > 1200)
        counter2_3 = 0;

      theta2c_3 = -(counter2_3 * 0.3);
    }

    if ( counter1_4 != temp1_4 ) {
      temp1_4 = counter1_4;

      if (counter1_4 > 1200)
        counter1_4 = 0;

      theta1c_4 = (counter1_4 * 0.3);
    }

    if ( counter2_4 != temp2_4 ) {
      temp2_4 = counter2_4;

      if (counter2_4 > 1200)
        counter2_4 = 0;

      theta2c_4 = -(counter2_4 * 0.3);
    }


    if (atan(ye_1 / xe_1) > 0)
      alpha_1 = atan(ye_1 / xe_1) - 3.14159;

    else
      alpha_1 = atan(ye_1 / xe_1);

    if (atan(ye_3 / xe_3) > 0)
      alpha_3 = atan(ye_3 / xe_3) - PI;

    else
      alpha_3 = atan(ye_3 / xe_3);

    if (atan(ye_4 / xe_4) > 0)
      alpha_4 = atan(ye_4 / xe_4) - PI;

    else
      alpha_4 = atan(ye_4 / xe_4);

    //------------------------------------------------------11111111111111111111----------------------------------------------------------------

    theta1_1 = 57.2958 * (cosine_rule(l1, l2, sqrt(xe_1 * xe_1 + ye_1 * ye_1)) + alpha_1);
    theta2_1 = 57.2958 * (-3.14159 + cosine_rule(sqrt(xe_1 * xe_1 + ye_1 * ye_1), l1, l2));

    error1_1 = theta1_1 - theta1c_1 + 53.728;
    error2_1 = theta2_1 - theta2c_1 / 4 + 42.68;

    dif_error1_1 = error1_1 - prev_error1_1;
    dif_error2_1 = error2_1 - prev_error2_1;

    c1_1 = (Kp1 - 0.5) * error1_1 + (Kd1 + 0.5) * (dif_error1_1);
    c2_1 = Kp2 * error2_1 + Kd2 * (dif_error2_1);

    prev_error1_1 = error1_1;
    prev_error2_1 = error2_1;

    correction1_1 = map(abs(c1_1), 0, 35, 0, 90);       //40 // 30
    correction2_1 = map(abs(c2_1), 0, 40, 0, 175);      //35

    //-------------------------------------------------------------22222222222222222222---------------------------------------------------

    if (t < 0.5) {
      theta1_2 = (-1) * theta(theta1AT1_2, theta1_AT1_2, theta1__AT1_2, theta1AT2_2, theta1_AT2_2, theta1__AT2_2, t);
      theta2_2 = (-1) * theta(theta2AT1_2, theta2_AT1_2, theta2__AT1_2, theta2AT2_2, theta2_AT2_2, theta2__AT2_2, t);
    }
    else {
      theta1_2 = (-1) * theta(theta1AT2_2, theta1_AT2_2, theta1__AT2_2, theta1AT3_2, theta1_AT3_2, theta1__AT3_2, t - 0.5);
      theta2_2 = (-1) * theta(theta2AT2_2, theta2_AT2_2, theta2__AT2_2, theta2AT3_2, theta2_AT3_2, theta2__AT3_2, t - 0.5);
    }

    error1_2 = theta1_2 - theta1c_2 + 65.8795;
    error2_2 = theta2_2 - theta2c_2 / 4 + 50.4;

    dif_error1_2 = error1_2 - prev_error1_2;
    dif_error2_2 = error2_2 - prev_error2_2;

    if (t < 0.5)
      c1_2 = (Kp1 - 0.5) * error1_2 + Kd1 * (dif_error1_2);
    else
      c1_2 = (Kp1 - 0.9) * error1_2 + Kd1 * (dif_error1_2);
    c2_2 = Kp2 * error2_2 + Kd2 * (dif_error2_2);

    prev_error1_2 = error1_2;
    prev_error2_2 = error2_2;

    correction1_2 = map(abs(c1_2), 0, 70, 0, 80 );
    if (t < 0.5)
      correction2_2 = map(abs(c2_2), 0, 90, 0, 200);
    else
      correction2_2 = map(abs(c2_2), 0, 90, 0, 210);

    //----------------------------------------------3333333333333333333333--------------------------------------------------------------------

    theta1_3 = 57.2958 * (cosine_rule(l2, l1, sqrt((xe_3 * xe_3) + (ye_3 * ye_3))) + alpha_3);
    theta2_3 = 57.2958 * (-3.14159 + cosine_rule(sqrt(xe_3 * xe_3 + ye_3 * ye_3), l1, l2));


    error1_3 = theta1_3 - theta1c_3 + 62.513;
    error2_3 = theta2_3 - theta2c_3 / 4 + 51.58;

    dif_error1_3 = error1_3 - prev_error1_3;
    prev_error1_3 = error1_3;
    dif_error2_3 = error2_3 - prev_error2_3;
    prev_error2_3 = error2_3;

    c1_3 = (Kp1 - 0.5) * error1_3 + (Kd1 + 0.5) * (dif_error1_3);
    c2_3 = Kp2 * error2_3 + Kd2 * (dif_error2_3);

    correction1_3 = map(abs(c1_3), 0, 30, 0, 50); //50
    correction2_3 = map(abs(c2_3), 0, 35, 0, 150);//175

    //----------------------------------------------------44444444444444444444-----------------------------------------------------------------------

    theta1_4 = 57.2958 * (cosine_rule(l2, l1, sqrt((xe_4 * xe_4) + (ye_4 * ye_4))) + alpha_4);
    theta2_4 = 57.2958 * (-3.14159 + cosine_rule(sqrt(xe_4 * xe_4 + ye_4 * ye_4), l1, l2));

    error1_4 = theta1_4 - theta1c_4 + 72.815;
    error2_4 = theta2_4 - theta2c_4 / 4 + 49.55;

    dif_error1_4 = error1_4 - prev_error1_4;
    prev_error1_4 = error1_4;
    dif_error2_4 = error2_4 - prev_error2_4;
    prev_error2_4 = error2_4;

    c1_4 = (Kp1 - 0.5) * error1_4 + (Kd1 + 0.5) * (dif_error1_4);
    c2_4 = Kp2 * error2_4 + Kd2 * (dif_error2_4);

    correction1_4 = map(abs(c1_4), 0, 30, 0, 50);     //50
    correction2_4 = map(abs(c2_4), 0, 35, 0, 150);    //175

    Serial.print("x=");
    Serial.println(xe_1);
    Serial.print("y=");
    Serial.println(ye_1);
    Serial.print("theta1_1=");
    Serial.println(theta1_1);
    Serial.print("theta1c_1=");
    Serial.println(theta1c_1 - 53.728);
    Serial.print("theta2c_1=");
    Serial.println(theta2c_1 - 42.68);
    Serial.print("theta2_1=");
    Serial.println(theta2_1);
    Serial.print("c1_1=");
    Serial.println(c1_1);
    Serial.print("c2_1=");
    Serial.println(c2_1);
    Serial.print("pwm1=");
    Serial.println(correction1_1);
    Serial.print("pwm2=");
    Serial.println(correction2_1);
    Serial.println("------------------------");


    if (error1_1 < 0 ) {
      upr_mtr_fwd_1();
      analogWrite(motor1pwm_1, abs(correction1_1));
    }

    else if (error1_1 > 0) {
      upr_mtr_bwd_1();
      analogWrite(motor1pwm_1, abs(correction1_1));
    }

    if (error2_1 < 0) {
      lwr_mtr_fwd_1();
      analogWrite(motor2pwm_1, abs(correction2_1));
    }

    else if (error2_1 > 0) {
      lwr_mtr_bwd_1();
      analogWrite(motor2pwm_1, abs(correction2_1));
    }

    if (error1_2 < 0 ) {
      upr_mtr_fwd_2();
      analogWrite(motor1pwm_2, abs(correction1_2));
    }

    else if (error1_2 > 0) {
      upr_mtr_bwd_2();
      analogWrite(motor1pwm_2, abs(correction1_2));
    }

    if (error2_2 < 0) {
      lwr_mtr_fwd_2();
      analogWrite(motor2pwm_2, abs(correction2_2));
    }

    else if (error2_2 > 0) {
      lwr_mtr_bwd_2();
      analogWrite(motor2pwm_2, abs(correction2_2));
    }

    if (error1_3 < 0 ) {
      upr_mtr_fwd_3();
      analogWrite(motor1pwm_3, abs(correction1_3));
    }

    else if (error1_3 > 0) {
      upr_mtr_bwd_3();
      analogWrite(motor1pwm_3, abs(correction1_3));
    }

    if (error2_3 < 0) {
      lwr_mtr_fwd_3();
      analogWrite(motor2pwm_3, abs(correction2_3));
    }

    else if (error2_3 > 0) {
      lwr_mtr_bwd_3();
      analogWrite(motor2pwm_3, abs(correction2_3));
    }

    if (error1_4 < 0 ) {
      upr_mtr_fwd_4();
      analogWrite(motor1pwm_4, abs(correction1_4));
    }

    else if (error1_4 > 0) {
      upr_mtr_bwd_4();
      analogWrite(motor1pwm_4, abs(correction1_4));
    }

    if (error2_4 < 0) {
      lwr_mtr_fwd_4();
      analogWrite(motor2pwm_4, abs(correction2_4));
    }

    else if (error2_4 > 0) {
      lwr_mtr_bwd_4();
      analogWrite(motor2pwm_4, abs(correction2_4));
    }

  }

  for (double t = 0.1666, u = 0.887; t < 1, u < 5.333; t = t + 0.1666, u = u + 0.887)
  {

    double xe_1 = 1.3333 + u ;
    double ye_1 = -45;

    double xe_2 = -6 + u;
    double ye_2 = -45;

    double xe_4 = 4.66 + u ;
    double ye_4 = -45;

    if ( counter1_1 != temp1_1 ) {
      temp1_1 = counter1_1;

      if (counter1_1 > 1200)
      {
        counter1_1 = 0;
      }
      theta1c_1 = (counter1_1 * 0.3);
    }

    if ( counter2_1 != temp2_1 ) {
      temp2_1 = counter2_1;

      if (counter2_1 > 1200)
      {
        counter2_1 = 0;
      }
      theta2c_1 = (counter2_1 * 0.3);
    }

    if ( counter1_2 != temp1_2 ) {
      temp1_2 = counter1_2;

      if (counter1_2 > 1200) {
        counter1_2 = 0;
      }
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

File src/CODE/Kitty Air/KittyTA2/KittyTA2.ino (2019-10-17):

#define motor1_3  27                 
#define motor2_3  26
#define motor1pwm_3  3
#define motor2pwm_3  2

#define motor1_4  36
#define motor2_4  29
#define motor1pwm_4  5
#define motor2pwm_4  4

#include <SoftwareSerial.h>

SoftwareSerial mySerial1(10, 11); // RX, TX          

int bb=1;

float w = 0.1, alpha_3, theta1c_3 = 0.0 , theta2c_3 = 0.0, theta1_3, theta2_3, error1_3, error2_3, correction1_3, correction2_3, c1_3, c2_3;
float dif_error1_3 , prev_error1_3 = 0.0 , dif_error2_3 , prev_error2_3 = 0.0;

float alpha_4, theta1c_4 = 0.0 , theta2c_4 = 0.0, theta1_4, theta2_4, error1_4, error2_4, correction1_4, correction2_4, c1_4, c2_4;
float dif_error1_4 , prev_error1_4 = 0.0 , dif_error2_4 , prev_error2_4 = 0.0;

float Kp1 = 1.5, Kp2 = 1.5, Kd1 = 2.0, Kd2 = 2.0 ;

int l1 = 25, l2 = 25, a = 20, b = 7;

volatile int temp1_3 , counter1_3 = 0;
volatile int temp2_3 , counter2_3 = 0;

volatile int temp1_4 , counter1_4 = 0;
volatile int temp2_4 , counter2_4 = 0;

void setup()
{
  Serial.begin(9600);
  mySerial1.begin(9600);

//  LEG-3

  pinMode(21, INPUT_PULLUP);                                           
  pinMode(6, INPUT_PULLUP);
  attachInterrupt(2, ai2_3, RISING);
  
  pinMode(20, INPUT_PULLUP);
  pinMode(7, INPUT_PULLUP);
  attachInterrupt(3, ai3_3, RISING);

  pinMode(motor1_3, OUTPUT);
  pinMode(motor1pwm_3, OUTPUT);
  pinMode(motor2_3, OUTPUT);
  pinMode(motor2pwm_3, OUTPUT);

  // LEG-4
  
  pinMode(19, INPUT_PULLUP);                                           
  pinMode(8, INPUT_PULLUP);
  attachInterrupt(4, ai4_4, RISING);
  
  pinMode(18, INPUT_PULLUP);
  pinMode(9, INPUT_PULLUP);
  attachInterrupt(5, ai5_4, RISING);

  pinMode(motor1_4, OUTPUT);
  pinMode(motor1pwm_4, OUTPUT);
  pinMode(motor2_4, OUTPUT);
  pinMode(motor2pwm_4, OUTPUT);

}

void loop()
{
    for (float u = 0.887; u < 10.666 ; u = u + 0.887)    
    {

      float xe_4 = -6 + u ;
      float ye_4 = -45;

      float xe_3 = 1.3333 + u ;
      float ye_3 = -45 ;

      if ( counter1_3 != temp1_3 )
      {
        temp1_3 = counter1_3;

        if (counter1_3 > 600)
          counter1_3 = 0;

        theta1c_3 = (counter1_3 * 0.6);
      }

      if ( counter2_3 != temp2_3 )
      {
        temp2_3 = counter2_3;

        if (counter2_3 > 600)
          counter2_3 = 0;

        theta2c_3 = -(counter2_3 * 0.6);
      }

      if ( counter1_4 != temp1_4 )
      {
        temp1_4 = counter1_4;

        if (counter1_4 > 600)
          counter1_4 = 0;

        theta1c_4 = (counter1_4 * 0.6);
      }

      if ( counter2_4 != temp2_4 )
      {
        temp2_4 = counter2_4;

        if (counter2_4 > 600)
          counter2_4 = 0;

        theta2c_4 = -(counter2_4 * 0.6);
      }


     
        if (atan(ye_3 / xe_3) > 0)
          alpha_3 = atan(ye_3 / xe_3) - PI;

        else
          alpha_3 = atan(ye_3 / xe_3);

        if (atan(ye_4 / xe_4) > 0)
          alpha_4 = atan(ye_4 / xe_4) - PI;

        else
          alpha_4 = atan(ye_4 / xe_4);
      


     
        theta1_3 = 57.2958 * (cosine_rule(l2, l1, sqrt((xe_3 * xe_3) + (ye_3 * ye_3))) + alpha_3);
        theta2_3 = 57.2958 * (-3.14159 + cosine_rule(sqrt(xe_3 * xe_3 + ye_3 * ye_3), l1, l2));

        error1_3 = theta1_3 - theta1c_3 + 62.513;        
        error2_3 = theta2_3 - theta2c_3/4 + 51.58;           

        dif_error1_3 = error1_3 - prev_error1_3;
        prev_error1_3 = error1_3;
        dif_error2_3 = error2_3 - prev_error2_3;
        prev_error2_3 = error2_3;

        c1_3 = Kp1 * error1_3 + Kd1 * (dif_error1_3);
        c2_3 = Kp2 * error2_3 + Kd2 * (dif_error2_3);

        correction1_3 = map(abs(c1_3), 0, 30, 0, 45); //50
        correction2_3 = map(abs(c2_3), 0, 35, 0, 125);//175

//        Serial.print("x=");
//        Serial.println(xe_3);       
//        Serial.print("y=");
//        Serial.println(ye_3);
//        Serial.print("theta1_3=");
//        Serial.println(theta1_3);
//        Serial.print("theta1c_3=");
//        Serial.println(theta1c_3-62.513);
//        Serial.print("theta2c_3=");
//        Serial.println(theta2c_3-51.58);        
//        Serial.print("theta2_3=");
//        Serial.println(theta2_3);
//        Serial.print("c1_3=");
//        Serial.println(c1_3);
//        Serial.print("c2_3=");
//        Serial.println(c2_3);
//        Serial.print("pwm1=");
//        Serial.println(correction1_3);
//        Serial.print("pwm2=");
//        Serial.println(correction2_3);
//        Serial.println("------------------------");

        theta1_4 = 57.2958 * (cosine_rule(l2, l1, sqrt((xe_4 * xe_4) + (ye_4 * ye_4))) + alpha_4);
        theta2_4 = 57.2958 * (-3.14159 + cosine_rule(sqrt(xe_4 * xe_4 + ye_4 * ye_4), l1, l2));

        error1_4 = theta1_4 - theta1c_4 + 72.815;         
        error2_4 = theta2_4 - theta2c_4/4 + 49.55;              

        dif_error1_4 = error1_4 - prev_error1_4;
        prev_error1_4 = error1_4;
        dif_error2_4 = error2_4 - prev_error2_4;
        prev_error2_4 = error2_4;

        c1_4 = Kp1 * error1_4 + Kd1 * (dif_error1_4);
        c2_4 = Kp2 * error2_4 + Kd2 * (dif_error2_4);

        correction1_4 = map(abs(c1_4), 0, 30, 0, 70);     //50
        correction2_4 = map(abs(c2_4), 0, 35, 0, 175);    //175
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
